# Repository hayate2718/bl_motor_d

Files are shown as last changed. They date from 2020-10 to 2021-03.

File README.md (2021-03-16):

# ブラシレスモータドライバー基板
## 機能
1. FETはTO252であれば使える。ゲート抵抗とゲートソース間コンデンサを調整すること<br>
ゲートソース間コンデンサは くらいになるようにする。
2. vdsth_pinで短絡検出を行う。パルス電流の絶対最大定格時の電圧降下を入れればいいと思う。計算式は下記 


3. ref_pinで定常の電流制限を行う。計算式は下記 


4. ピンヘッダをショートすることで動作モードの切り替えが可能<br>
jp1がfフラグを無視（オープンループでリミットを完全に外す場合はさらにRCピンをショートしてください）、jp2が高速減衰モードにできる(動くときと動かんときがある)
5. untitl.txtファイルは読んでください<br>
## 制作者コメント
<b>一枚の値段がいくらになるのか考えたくもない...結果としては4000yenほど(たけぇ<br>
このMDは制御方法が台形120度通電であるため低速域よりも高速域の効率のほうが良い。<br>
モータの最大効率運転では電流波形が正弦波に近いほどよく、台形120度通電では電流波形が台形になるように制御されているが高速域では電流波形が正弦波に近くなるため効率が良くなる。</b>

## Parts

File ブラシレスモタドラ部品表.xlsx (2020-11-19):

ブラシレスモータードライバ部品リスト
部品名 | 必要個数 | 買う場所 | 必要価格 | 単価 | 最低個数価格 | 備考(通販のコードとか)
半導体
a3930 | 1 | digikey | 722 | 722 | 722 | 620-1289-1-ND
2sc5964 | 1 | rs | 46.5 | 46.5 | 465 | 774-0746
ipd034n06ngatma1 | 6 | rs | 948 | 158 | 1580 | 825-9168
ss2040 | 1 | 秋月電子 | 15 | 15 | 300 | i02073
フルカラーRGBled | 1 | 秋月電子 | 10 | 10 | 100 | I-12726
SBR10M100P5Q | 6 | digikey | 462 | 77 | 77 | SBR10M100P5Q-13DICT-ND
ES3BB-13-F | 6 | digikey | 420 | 70 | 70 | ES3BB-FDICT-ND
fdc6305 | 1 | 秋月電子 | 12 | 12 | 120 | I-06003
抵抗 |  |  | 0
10k(1608) | 10 |  | 0
10k(集合) | 1 | 秋月電子 | 1 | 1 | 100 | p04664
47k(1608) | 2 |  | 0
39k(1608) | 1 |  | 0
22k(1608) | 1 |  | 0
33k(1608) | 2 |  | 0
1k(集合) | 1 |  | 0
10(1608) | 6 |  | 0
22(1206) | 6 | rs | 168 | 28 | 138 | 721-9680
20m(2512) | 4 | rs | 308.8 | 77.2 | 386 | 693-4384
0(1608) | 1 | 秋月電子 | 0 |  | 100 | R-11619
コンデンサ |  |  | 0
0.1u | 3 |  | 0
10u | 2 | 秋月電子 | 30 | 15 | 150 | P-13161
0.22u | 4 | 秋月電子 | 4 | 1 | 100 | P-05622
2.2u | 2 | 秋月電子 | 20 | 10 | 100 | P-14788
0.47u | 1 | 秋月電子 | 5 | 5 | 100 | 無ければP-14526これ使って
680p | 1 | 秋月電子 | 1.8 | 1.8 | 180 | P-09273
820u | 1 | rs | 107 | 107 | 535 | 843-2168
4.7n | 6 | 秋月電子 | 0 |  | 100 | P-14552
フィルムコンデンサ0.33u | 6 | rs | 156 | 26 | 660 | 896-1329
コネクタ |  |  | 0
vl3p | 1 | digikey | 111 | 111 | 111 | 455-2362-ND
xt60 | 1 | amazon | 0
ロングピンソケット8p | 2 | 秋月電子 | 0 |  | 80 | C-05779
ピンヘッダ2p | 2 | 秋月電子 | 0
zh6p L型 | 1 | 秋月電子 | 0
xh2p | 1 | 秋月電子 | 0
最低価格 |  |  | 3548.1
ブラシレスモタドラインターフェース
半導体
tlp291 | 1 | 秋月電子 | 20 | 20 | 20 | I-07189
tlp2395 | 2 | rs | 219 | 109.5 | 1095 | 885-1171
tlp290 | 1 | rs | 118 | 118 | 1180 | 885-1083
ss2040 | 1 | 秋月電子 | 15 | 15 | 300 | i02073
抵抗 |  |  | 0
1k(1608) | 10 |  | 0
4.7k(1608) | 2 |  | 0
9.1k(1608) | 2 | rs | 6.92 | 3.46 | 173 | 631-6626
コンデンサ |  |  | 0
0.1u | 3 |  | 0
コネクタ |  |  | 0
ピンヘッダ8p | 2 | 秋月電子 | 0
df1b4p | 1 |  | 0
df1b6p | 1 |  | 0
 |  |  | 378.92 |  | 9042

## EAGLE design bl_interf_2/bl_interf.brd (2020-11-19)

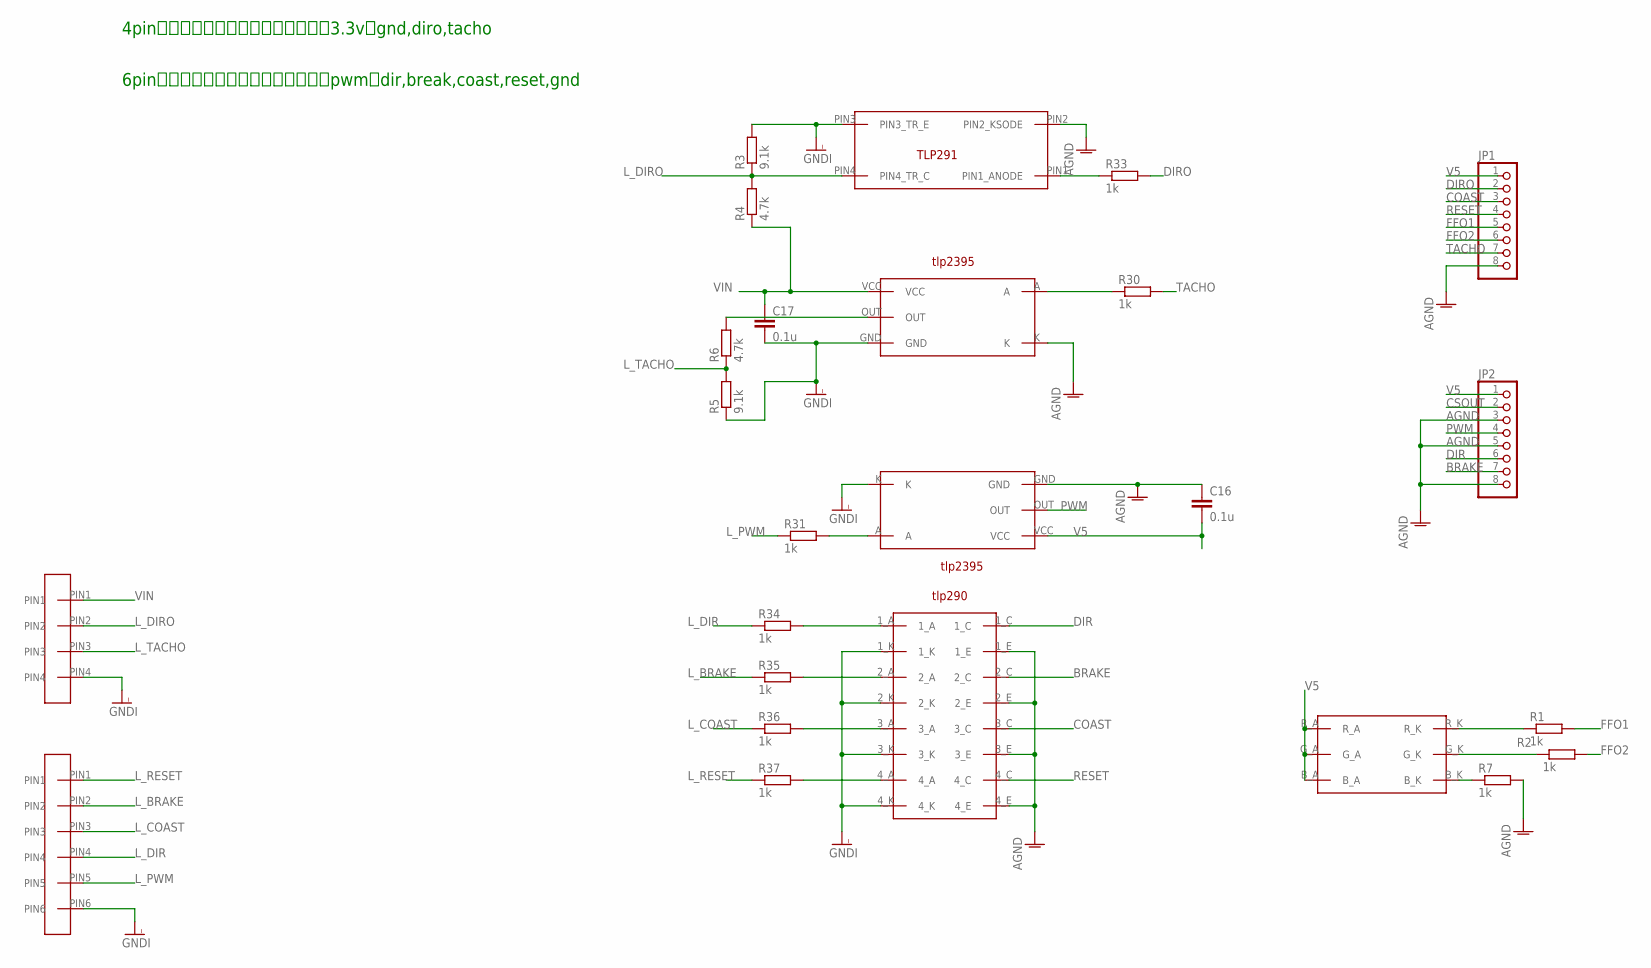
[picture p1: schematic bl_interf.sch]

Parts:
C16, C17: 0.1u; C2012
JP1, JP2: PINHD-1X8; 1X08
R1, R2, R7, R30, R31, R33, R34, R35, R36, R37: 1k; M2012
R3, R5: 9.1k; M2012
R4, R6: 4.7k; M2012
U$1: RGB_LED
U$17, U$18: TLP2395
U$19: TLP291
U$20: TLP290-4; TLP290
U$21: DF1B_L_4P
U$22: DF1B_L_6P

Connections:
AGND: C16.1, JP1.8, JP2.3, JP2.5, JP2.8, R7.2, U$17.K, U$18.GND, U$19.PIN2 (PIN2_KSODE), U$20.1_E, U$20.2_E, U$20.3_E, U$20.4_E
BRAKE: JP2.7, U$20.2_C
COAST: JP1.3, U$20.3_C
CSOUT: JP2.2
DIR: JP2.6, U$20.1_C
DIRO: JP1.2, R33.2
FFO1: JP1.5, R1.2
FFO2: JP1.6, R2.2
GNDI: C17.2, R3.2, R5.1, U$17.GND, U$18.K, U$19.PIN3 (PIN3_TR_E), U$20.1_K, U$20.2_K, U$20.3_K, U$20.4_K, U$21.PIN4, U$22.PIN6
L_BRAKE: R35.1, U$22.PIN2
L_COAST: R36.1, U$22.PIN3
L_DIR: R34.1, U$22.PIN4
L_DIRO: R3.1, R4.2, U$19.PIN4 (PIN4_TR_C), U$21.PIN2
L_PWM: R31.1, U$22.PIN5
L_RESET: R37.1, U$22.PIN1
L_TACHO: R5.2, R6.1, U$21.PIN3
unnamed: R7.1, U$1.B_K
unnamed: R1.1, U$1.R_K
unnamed: R2.1, U$1.G_K
unnamed: R30.1, U$17.A
unnamed: R31.2, U$18.A
unnamed: R6.2, U$17.OUT
unnamed: R34.2, U$20.1_A
unnamed: R33.1, U$19.PIN1 (PIN1_ANODE)
unnamed: R35.2, U$20.2_A
unnamed: R36.2, U$20.3_A
unnamed: R37.2, U$20.4_A
PWM: JP2.4, U$18.OUT
RESET: JP1.4, U$20.4_C
TACHO: JP1.7, R30.2
V5: C16.2, JP1.1, JP2.1, U$1.B_A, U$1.G_A, U$1.R_A, U$18.VCC
VIN: C17.1, R4.1, U$17.VCC, U$21.PIN1

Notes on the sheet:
4pinでモタドラからの出力を受ける。3.3vとgnd,diro,tacho
6pinでモタドラに対して入力を行う。pwmとdir,break,coast,reset,gnd

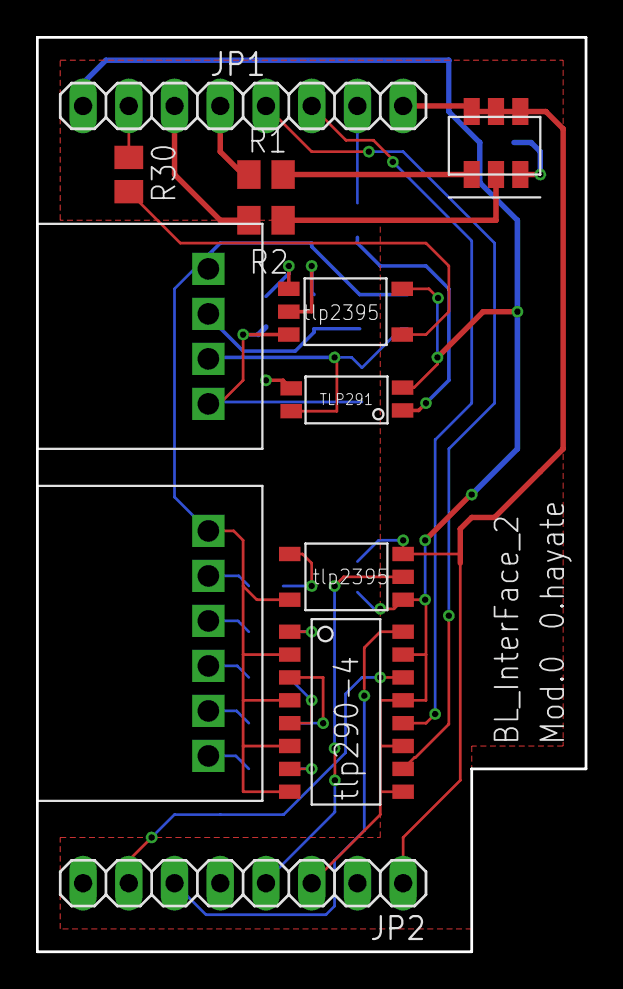
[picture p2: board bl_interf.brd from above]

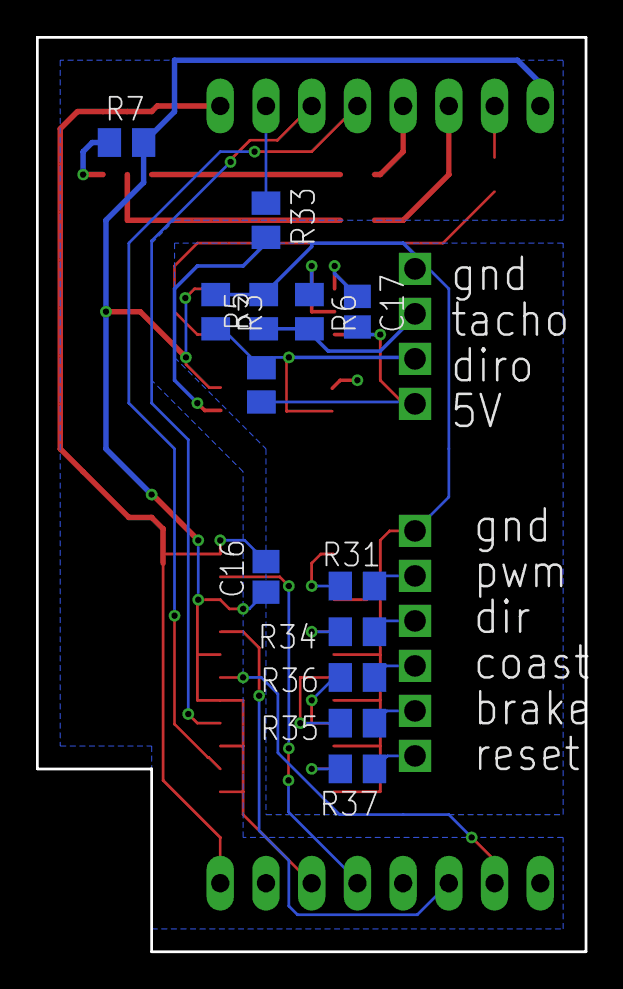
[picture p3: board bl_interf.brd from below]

Board: 2 copper layers, 30.5 x 50.8 mm, 25 parts (13 on the bottom side), 31 nets.

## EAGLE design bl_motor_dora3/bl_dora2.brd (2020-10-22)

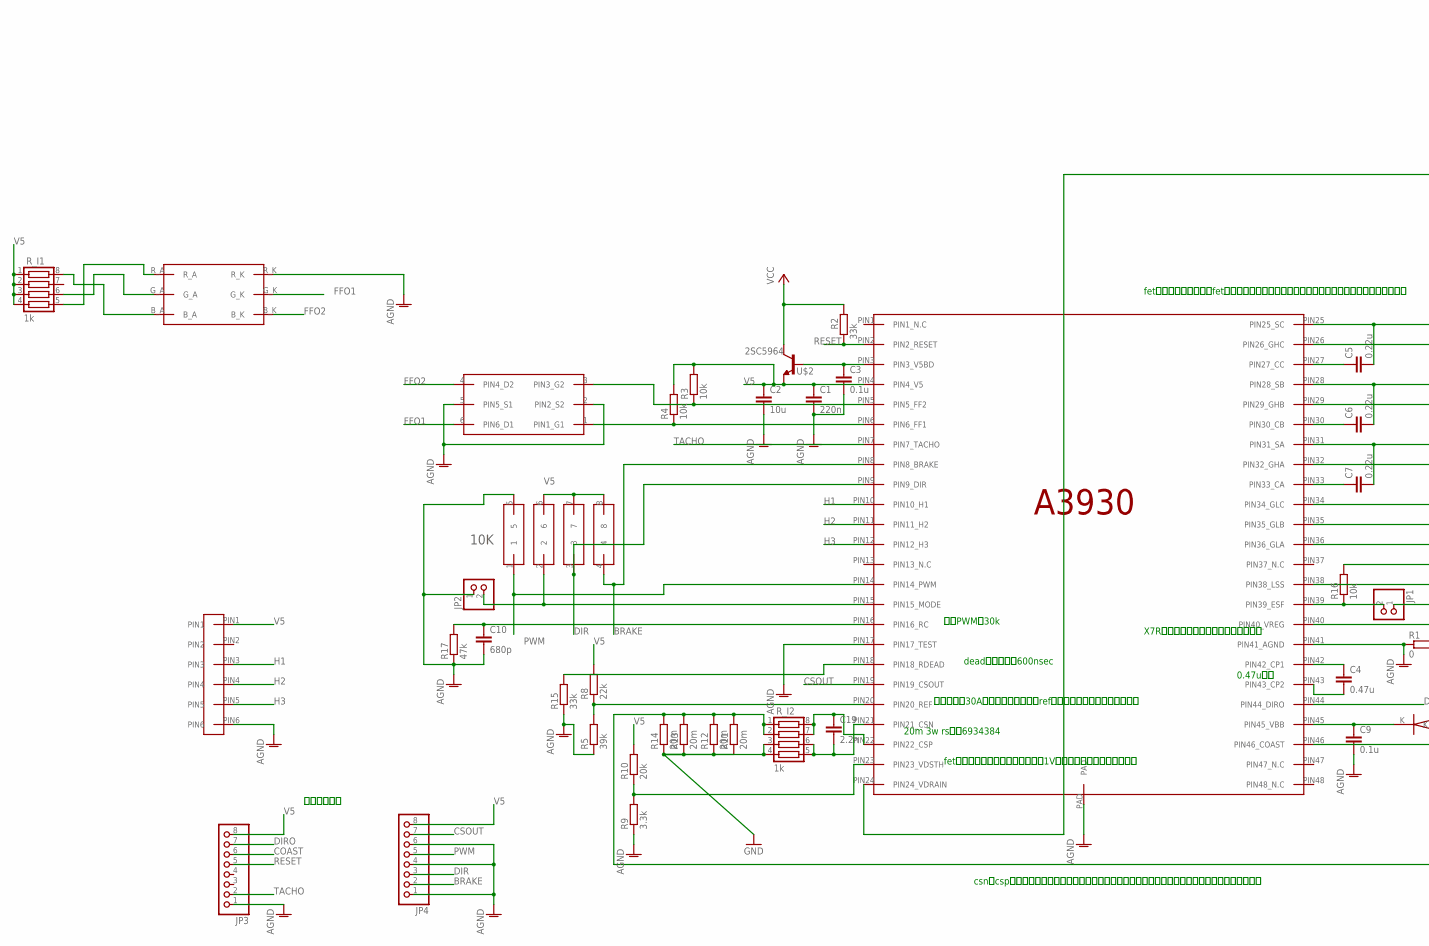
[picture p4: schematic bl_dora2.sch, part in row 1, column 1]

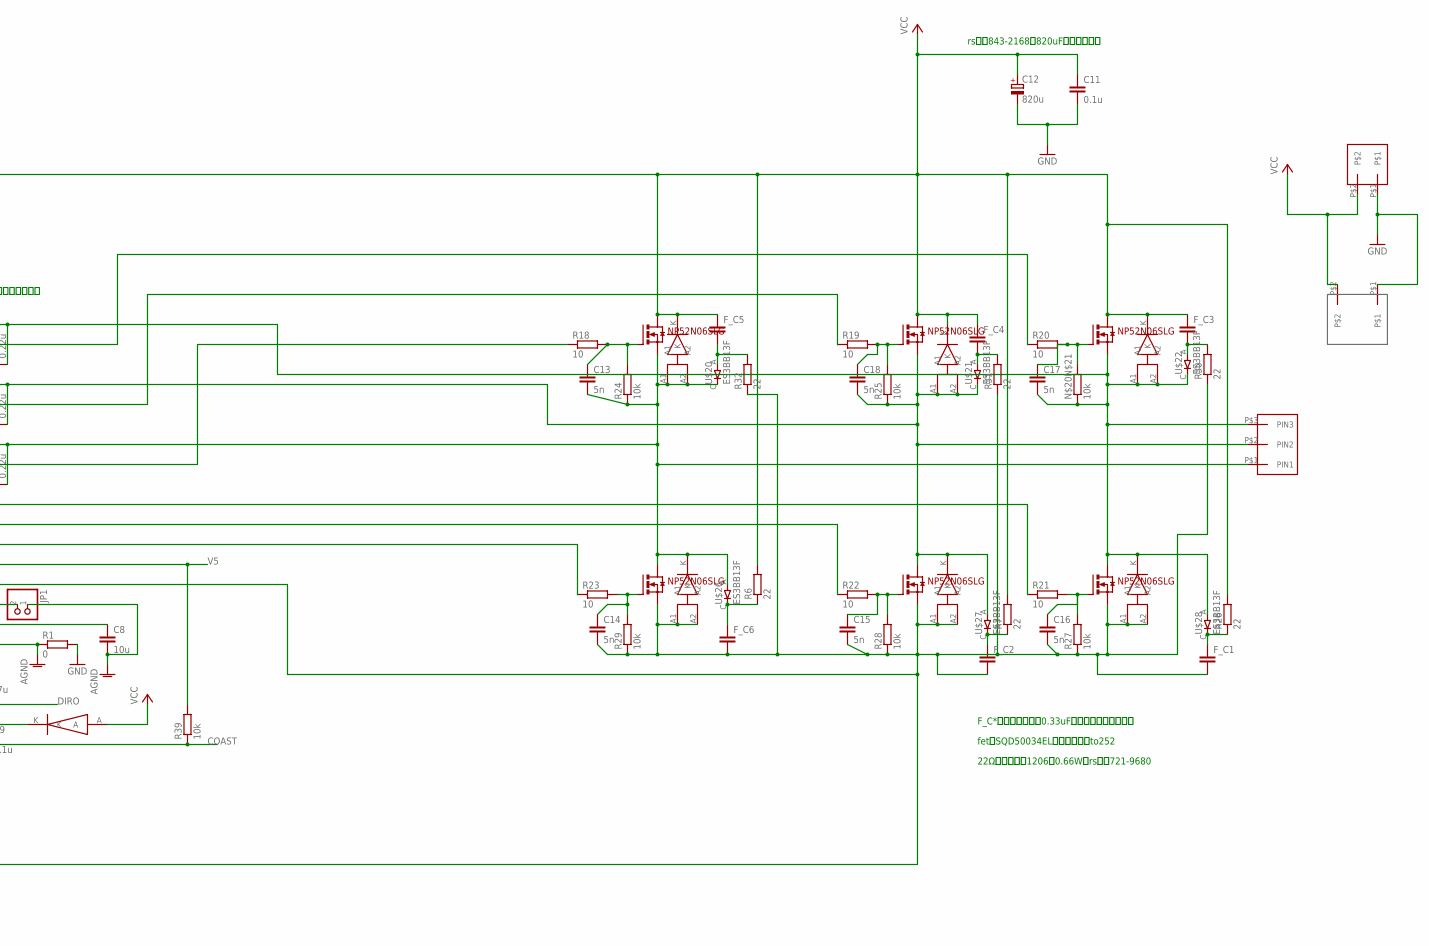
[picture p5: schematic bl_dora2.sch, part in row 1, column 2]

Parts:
C1: 220n; C2012
C2, C8: 10u; C2012
C3, C9, C11: 0.1u; C2012
C4: 0.47u; C2012
C5, C6, C7: 0.22u; C2012
C10: 680p; C2012
C12: 820u; 153CLV-1012
C13, C14, C15, C16, C17, C18: 5n; C2012
C19: 2.2n; C1608
F_C1, F_C2, F_C3, F_C4, F_C5, F_C6: FIL_CAPA
JP1, JP2: PINHD-1X2; 1X02
JP3, JP4: PINHD-1X8; 1X08
N$20N$21: 10k; M2012
R1: 0; M2012
R2, R15: 33k; M2012
R3, R4, R16, R24, R25, R27, R28, R29, R39: 10k; M2012
R5: 39k; M2012
R6, R7, R26, R30, R31, R32: 22; R1206
R8: 22k; M2012
R9: 3.3k; M2012
R10: 20k; M2012
R11, R12, R13, R14: 20m; R2512
R17: 47k; M2012
R18, R19, R20, R21, R22, R23: 10; M2012
R_I1, R_I2: 1k; 0603X4RESISTOR
U$1: A3930
U$2: 2SC5964
U$3: SSOT6_FET
U$4: RGB_LED
U$5: 10K; 1005X4RESISTOR
U$6: SMD_DAIOD
U$7, U$8, U$9, U$10, U$11, U$12: NP52N06SLG
U$13, U$14, U$15, U$16, U$17, U$18: SBR10M100P5Q
U$19: XH_2P
U$20, U$21, U$22, U$26, U$27, U$28: ES3BB13F
U$23: ZH_6P_L
U$24: XT60
U$25: VL_3P

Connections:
AGND: C1.2, C2.2, C3.2, C8.2, C9.2, C10.2, JP1.1, JP2.1, JP3.1, JP4.1, JP4.4, JP4.6, R1.1, R5.1, R9.1, R15.1, R17.1, U$1.PAD, U$1.PIN17 (PIN17_TEST), U$1.PIN41 (PIN41_AGND), U$3.2 (PIN2_S2), U$3.5 (PIN5_S1), U$4.R_K, U$5.5, U$23.PIN6
BRAKE: JP4.2, U$1.PIN8 (PIN8_BRAKE), U$5.4
COAST: JP3.6, R39.1, U$1.PIN46 (PIN46_COAST)
CSOUT: JP4.7, U$1.PIN19 (PIN19_CSOUT)
DIR: JP4.3, U$1.PIN9 (PIN9_DIR), U$5.3
DIRO: JP3.7, U$1.PIN44 (PIN44_DIRO)
ESF: JP1.2, R16.1, U$1.PIN39 (PIN39_ESF)
FFO1: U$3.6 (PIN6_D1), U$4.G_K
FFO2: U$3.4 (PIN4_D2), U$4.B_K
GND: C11.2, C12.-, R1.2, R11.1, R12.1, R13.1, R14.1, R_I2.3, R_I2.4, U$19.P$1, U$24.P$1
H1: U$1.PIN10 (PIN10_H1), U$23.PIN3
H2: U$1.PIN11 (PIN11_H2), U$23.PIN4
H3: U$1.PIN12 (PIN12_H3), U$23.PIN5
unnamed: C3.1, U$1.PIN3 (PIN3_V5BD), U$2.B
unnamed: R3.1, U$1.PIN5 (PIN5_FF2), U$3.3 (PIN3_G2)
unnamed: R4.1, U$1.PIN6 (PIN6_FF1), U$3.1 (PIN1_G1)
unnamed: R15.2, U$1.PIN18 (PIN18_RDEAD)
unnamed: F_C5.P$2 (2), R32.2, U$20.A
unnamed: C14.2, C15.2, C16.2, F_C1.P$2 (2), F_C2.P$2 (2), F_C6.P$2 (2), R11.2, R12.2, R13.2, R14.2, R27.1, R28.1, R29.1, R30.1, R31.1, R32.1, R_I2.1, R_I2.2, U$1.PIN38 (PIN38_LSS), U$8.PIN3_S, U$10.PIN3_S, U$12.PIN3_S, U$14.A1, U$14.A2, U$15.A1, U$15.A2, U$18.A1, U$18.A2
unnamed: R5.2, R8.1, U$1.PIN20 (PIN20_REF)
unnamed: C19.2, R_I2.5, R_I2.6, U$1.PIN21 (PIN21_CSN)
unnamed: R9.2, R10.1, U$1.PIN23 (PIN23_VDSTH)
unnamed: R_I1.5, U$4.R_A
unnamed: C4.1, U$1.PIN42 (PIN42_CP1)
unnamed: JP2.2, U$1.PIN15 (PIN15_MODE), U$5.2
unnamed: C4.2, U$1.PIN43 (PIN43_CP2)
unnamed: C5.1, U$1.PIN27 (PIN27_CC)
unnamed: C6.1, U$1.PIN30 (PIN30_CB)
unnamed: C7.1, U$1.PIN33 (PIN33_CA)
unnamed: C7.2, C13.2, R24.1, U$1.PIN31 (PIN31_SA), U$7.PIN3_S, U$8.PIN2_D, U$13.A1, U$13.A2, U$14.K, U$20.C, U$25.P$1 (PIN1), U$26.A
unnamed: C19.1, R_I2.7, R_I2.8, U$1.PIN22 (PIN22_CSP)
unnamed: R_I1.6, U$4.G_A
unnamed: C8.1, U$1.PIN40 (PIN40_VREG)
unnamed: C9.1, U$1.PIN45 (PIN45_VBB), U$6.K
unnamed: C10.1, R17.2, U$1.PIN16 (PIN16_RC)
unnamed: C13.1, R18.2, R24.2, U$7.PIN1_G
unnamed: C18.1, R19.2, R25.2, U$9.PIN1_G
unnamed: C17.1, N$20N$21.2, R20.2, U$11.PIN1_G
unnamed: C16.1, R21.2, R27.2, U$12.PIN1_G
unnamed: C15.1, R22.2, R28.2, U$10.PIN1_G
unnamed: C14.1, R23.2, R29.2, U$8.PIN1_G
unnamed: R23.1, U$1.PIN36 (PIN36_GLA)
unnamed: R22.1, U$1.PIN35 (PIN35_GLB)
unnamed: R21.1, U$1.PIN34 (PIN34_GLC)
unnamed: R_I1.8, U$4.B_A
unnamed: R18.1, U$1.PIN32 (PIN32_GHA)
unnamed: R19.1, U$1.PIN29 (PIN29_GHB)
unnamed: R20.1, U$1.PIN26 (PIN26_GHC)
unnamed: F_C4.P$2 (2), R31.2, U$21.A
unnamed: F_C3.P$2 (2), R30.2, U$22.A
unnamed: F_C6.P$1 (1), R6.1, U$26.C
unnamed: C5.2, C17.2, N$20N$21.1, U$1.PIN25 (PIN25_SC), U$11.PIN3_S, U$12.PIN2_D, U$17.A1, U$17.A2, U$18.K, U$22.C, U$25.P$3 (PIN3), U$28.A
unnamed: F_C1.P$1 (1), R26.1, U$28.C
unnamed: F_C2.P$1 (1), R7.1, U$27.C
unnamed: C6.2, C18.2, R25.1, U$1.PIN28 (PIN28_SB), U$9.PIN3_S, U$10.PIN2_D, U$15.K, U$16.A1, U$16.A2, U$21.C, U$25.P$2 (PIN2), U$27.A
PWM: JP4.5, U$1.PIN14 (PIN14_PWM), U$5.1
RESET: JP3.5, R2.1, U$1.PIN2 (PIN2_RESET)
TACHO: JP3.2, U$1.PIN7 (PIN7_TACHO)
V5: C1.1, C2.1, JP3.8, JP4.8, R3.2, R4.2, R8.2, R10.2, R16.2, R39.2, R_I1.1, R_I1.2, R_I1.3, R_I1.4, U$1.PIN4 (PIN4_V5), U$2.E, U$5.6, U$5.7, U$5.8, U$23.PIN1
VCC: C11.1, C12.+, F_C3.P$1 (1), F_C4.P$1 (1), F_C5.P$1 (1), R2.2, R6.2, R7.2, R26.2, U$1.PIN24 (PIN24_VDRAIN), U$2.C, U$2.C@2 (C), U$6.A, U$7.PIN2_D, U$9.PIN2_D, U$11.PIN2_D, U$13.K, U$16.K, U$17.K, U$19.P$2, U$24.P$2

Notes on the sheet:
20m 3w rs品番6934384
0.47u以上
deadタイムは約600nsec
内部PWMは30k
csnとcspはできるだけ同じ長さで同じルート・無理にくねくねさせるなら同じながさでなくていい
ピンソケット
X7Rなどの特性のよいものをつかうこと
fetを変えた場合はそのfetのゲート容量によってブートストラップコンデンサを変えること
rs品番843-2168の820uFのコンデンサ
F_C*のコンデンサは0.33uFのフィルムコンデンサ
fetにSQD50034ELを使う。同じto252
電流制限は30Aに設定されている。refの抵抗比を変えることで変更可
fetのドレインソース間がオン時に1Vを超えたら短絡とみなされる
22Ωの抵抗器は1206の0.66W。rs品番721-9680

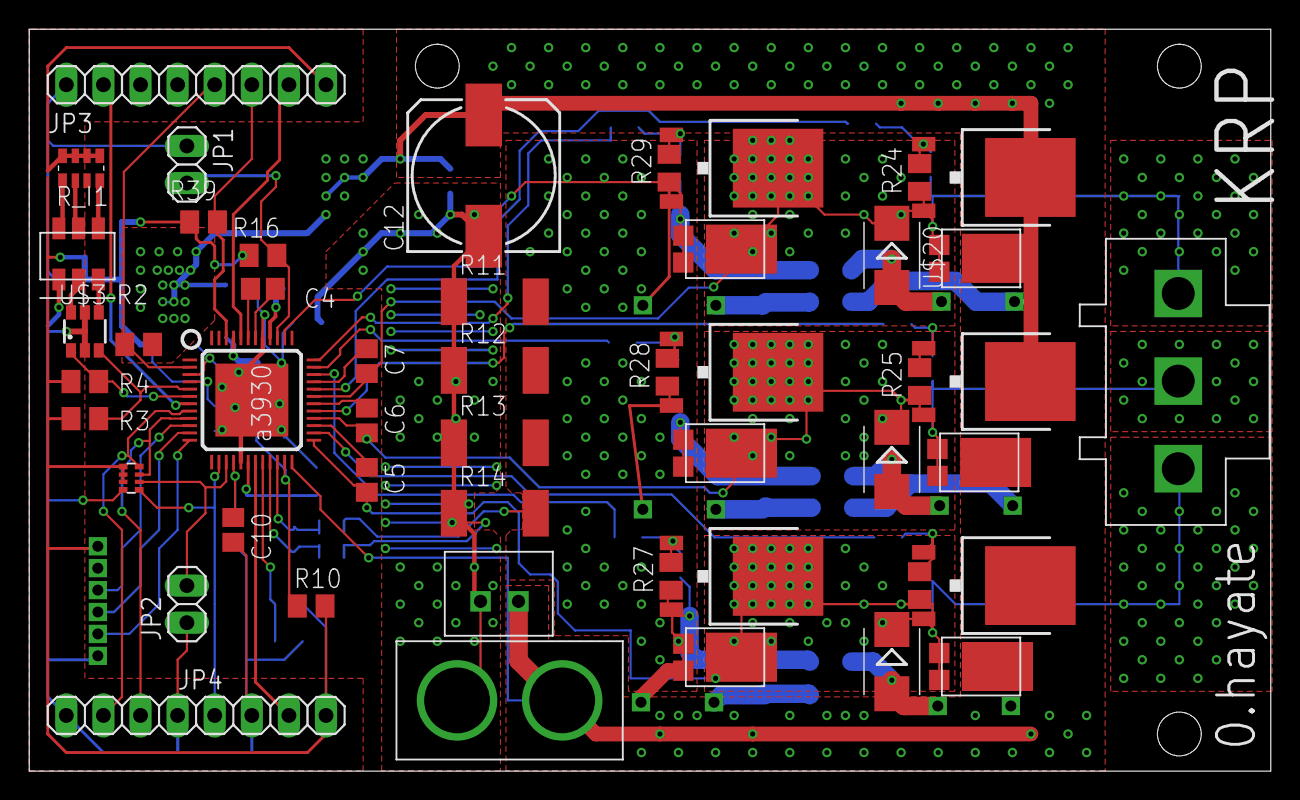
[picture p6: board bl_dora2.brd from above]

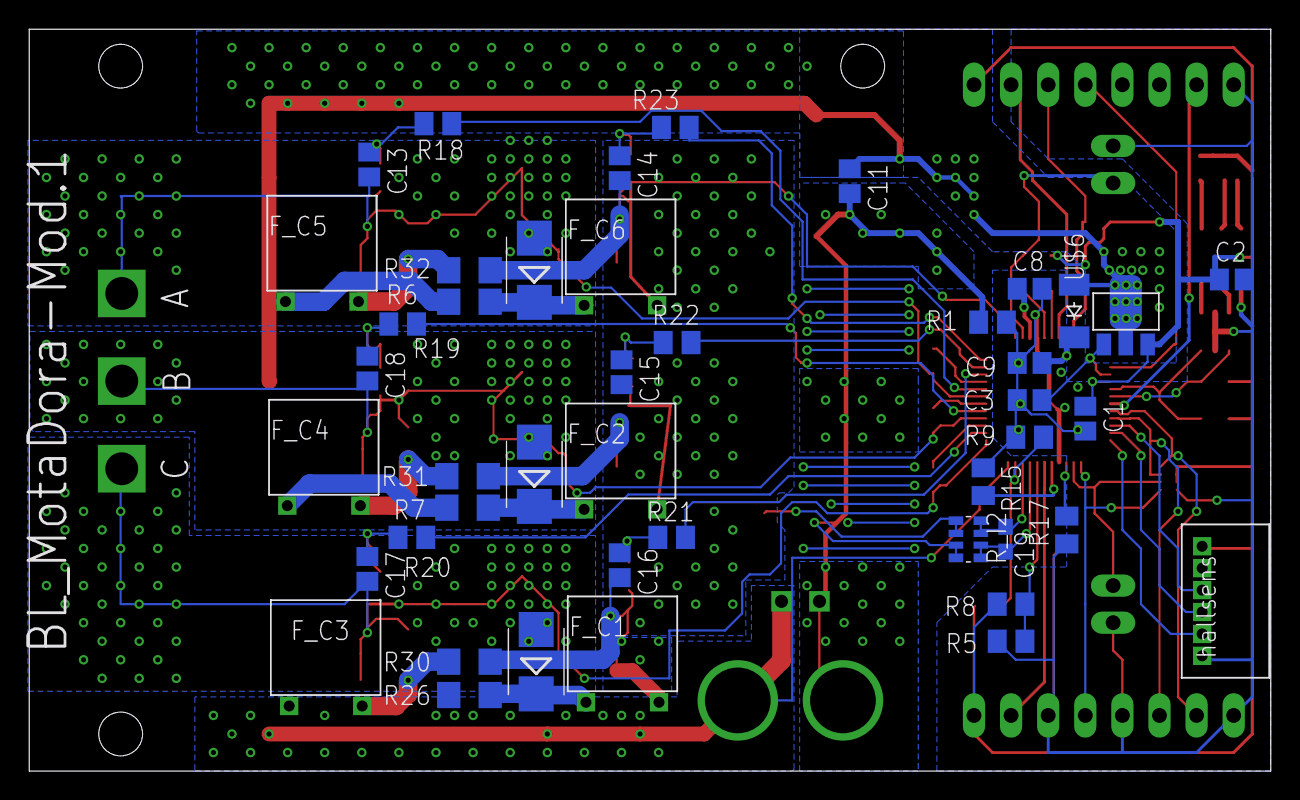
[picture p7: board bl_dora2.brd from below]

Board: 2 copper layers, 85.0 x 50.8 mm, 93 parts (44 on the bottom side), 60 nets.

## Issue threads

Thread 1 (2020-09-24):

基板固定用の穴がない

TakashiKusachi, 2020-09-24:
基板固定用の穴がないのは実用上かなり厳しい。
* 基盤がケーブルに引っ張られて飛ぶ。
* 「後でつける」は永遠とやらない（体験談）

最低でも三か所で固定できるようにした方がいいです。（二か所はその線を軸に回転がかかって固定側が壊れる）

TakashiKusachi, 2020-09-29:
ドリル穴3はM2にしてはでかいしM3にしては小さいから2.7mmとか2.3mmとかにした方がいい

Closed 2020-10-05.

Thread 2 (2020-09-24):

PWM周波数について

TakashiKusachi, 2020-09-24:
アバランシェ破壊したのでは？ということでしたが、一度確認したい点が一つ。
PWM周波数はいくつで設定しましたか？

BLDCの場合、PWM周波数が高くても低くてもMOSFETには危ないので気を付けてください。

hayate2718, 2020-09-25:
pwm周波数は50kHzです。理由としては、自分のpwm発生道具が50kHzでプログラム書き直すのめんどくさかったというのが大きかったのですが、a3930のデモボードの回路図をみて内部pwm周波数が40kHzで設定されており、外部pwmで動かすときは内部pwm周波数よりも高くするということだったので50kHzで問題ないだろうと判断しました。

hayate2718, 2020-09-25:
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

pwm周波数は50kHzです。理由としては、自分のpwm発生道具が50kHzでプログラム書き直すのめんどくさかったというのが大きかったのですが、a3930のデモボードの回路図をみて内部pwm周波数が40kHzで設定されており、外部pwmで動かすときは内部pwm周波数よりも高くするということだったので50kHzで問題ないだろうと判断しました。

TakashiKusachi, 2020-09-25:
なるほど。おおよそ問題ないかと。
Rgを大きくしたみたいなので、デッドタイムとの兼ね合いを気を付けてください。
軽く設計を見た限りt_deatが2.84(1.42 * 2)us、PWMが20um(50kHz)なので結構近くなってる。現状でduty10%未満はほとんど回らないことになっている。これだと低速回転時に安定しないので、設計を見直した方がいいかもしれない。

### Rgを大きくするときの注意
1. Rgを大きくする
2. スイッチングに時間がかかる
3. デッドタイムを大きくする必要がある。
4. PWM一周期あたりのデッドタイムの割合が増える
5. 低duty、高dutyの線形性がなくなる。
6. 制御性ポンコツ

対策
1. PWM周波数を下げる。
2. デッドタイムを短くする。

デッドタイムの設計はなんかの資料を参考にしてほしいですが、ゲートの挙動をオシロで見るのが早いです。ただ、オシロが使えない現状では、LTSpiceかなんかのシミュレータで挙動をみてもいいかもしれないですね。

TakashiKusachi, 2020-09-25:
追記で
先日の報告会でH氏から、フリーホイーリングダイオードについて聞かれてましたが、bodyDで済ませているという回答を聞きました。
電流の小さいアプリケーションではbodyDで問題ないです。が、電流の大きいアプリケーションでは、少し問題が現れます。

まず、bodyDはフリーホイーリングのためにあるわけではないという認識をもってほしいです（あれはMOSFETの構造上表れているだけ）。このため、フリーホイーリングの目的に対応した特性としては糞です。重要な特性は二つ（というよりこれ以外書いてないけど
* 逆回復時間
* Vf（順方向起電圧）

デッドタイム中はこのフリーホイーリングDを通って電流が還ります。このため、Vfが大きいとその分損失が大きいことになります。またデッドタイムからローサイドをオープンするとき、ハイサイドのDは順方向（S->D)から逆方向へと電圧が変わるわけですが、この時結構電流が流れます。この時間が逆回復時間です。つまりハイサイドとローサイドが両方ともオープンになる貫通の時間があって、これがローサイドを大きく発熱させます。

長くなりましたが、bodyDはそこまで気を遣った特性ではないためこの点を注意した方がいいということです。逆回復時間は電流に相関があるため、電流が小さい限りは問題ないです。

以上知っていたら、長文失礼しました。

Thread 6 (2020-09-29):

シャントの配線があまりよろしくない

TakashiKusachi, 2020-09-29:
## 低抵抗シャントでの電流測定の配線があまりよろしくない
低抵抗の電流計測はアナログ回路としてかなり丁寧に設計しないと実はろくに使えたものじゃないので注意してください。

### 抵抗器と分岐点の間にできるだけ電流を流さないこと
電流測定に重要なことは信用できる抵抗値であり、これを達成するにはパターンの抵抗自体考慮する必要があります。このため下図のように、電流が流れるルートから切り離して測定用のパターンを伸ばす必要があります。
少し話は変わってしまいますが、４端子抵抗測定法などを調べてみると勉強になるかも
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
この距離が良くないという話。
### ただし、そもそも抵抗器が5%...
なので気にしなくてもいいかも。

## 配線の長さをそろえる部分について
多分いらない。配線の長さをそろえるのは、主にデジタルの高速信号の場合だけです。配線長の偏差が信号の周期の定数倍以上になると周期がずれて信号が正確に読み取れなくなりますが、アナログで低速である限りは必要ないです。
また、上の話を考慮したくなるかもしれないですが、この信号線に流れる電流は微量（入力インピーダンスが高い）です。なので、配線の長さをそろえてインピーダンスをそろえる必要はないです。一方で電流が小さいからこそ、ノイズに弱い信号線になります。下手にくねくねさせた方が危ない。

TakashiKusachi, 2020-09-29:
追記。データシートにながさ揃えろって書いてあるのか…
こんな露骨にくねくねさせるよりは、自然に長さがそろうようにした方がいいかと。図のような配線なら勝手に合うはず

hayate2718, 2020-09-29:
測定点までの距離を同じくらいにするために0Ω抵抗を使って測定用の配線を作ってみます。くねくねさせて無理やりそろえるくらいだったら多少の誤差は無視したほうが良いですか？

TakashiKusachi, 2020-09-29:
0オーム？

多少はね。無視してもいいんじゃないかな

Closed 2020-10-05.

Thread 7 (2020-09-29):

RCDスナバのDについて

TakashiKusachi, 2020-09-29:
## RCDスナバのDはショットキーバリア(SBD)よりpn接合型ダイオードの方がいいと思う
RCDスナバのDとしては逆回復特性や降伏電圧の高いpn接合のD（ファストリカバリーダイオード(FRD)と呼ばれている種類）の方がいいはずなのでそれに変えた方がいいと思います。それからスナバ回路にはそんな大電流流れないのでもっと小さいのでも大丈夫では？

そもそもスナバいる？

hayate2718, 2020-09-29:
このダイオードの逆回復時間が18nsecで降伏電圧が100Vなのですが、具体的にどのくらいの逆回復時間と降伏電圧のものを選んだほうが良いですか？スナバ回路ってそんなに大電流流れないのですね...瞬間電流100Aほど流せるドライバにしたかったので瞬間電流の最大定格をその倍取っていました。スナバ回路はこれつけとけばfet保護は完璧だろうというノリでつけました。

TakashiKusachi, 2020-09-29:
こいつショットキーバリアダイオード（SBD)じゃなくてDIODES社商標のスーパーバリアダイオードとかいう特殊なやつなのか…
同様にSBDの代替で開発されたものみたいで、高逆回復特性、低vfが特徴みたいだけど、この用途なら低vfは必要ないからもう少し小さくて安いやつでも大丈夫じゃない？というコストのお話になる。それことフリーホイーリングD(FWD)がないのは問題なので、スナバにこんなデカい領域使うなら変えた方がいいと思う。

TakashiKusachi, 2020-09-29:
https://toshiba.semicon-storage.com/info/docget.jsp?did=13411
これ見てみた？

hayate2718, 2020-09-29:
一応見たことあります。スナバの設計に使った資料は添付した二つのファイルです。
[sic-mos_snubber_circuit_design_an-j.pdf](https://github.com/hayate2718/bl_motor_d/files/5301074/sic-mos_snubber_circuit_design_an-j.pdf)
[RH984b_05.pdf](https://github.com/hayate2718/bl_motor_d/files/5301075/RH984b_05.pdf)

hayate2718, 2020-09-29:
現在スナバに使ったダイオードはフリーホイールダイオードに使える性能していますか？一応スナバに関してはどの程度の電流が流れるのかわからなくてかなり多く見積もっていたので、電流がそれほど流れないのであればもともと採用しようとしていた小さいダイオードがあるのでそれを用います。

TakashiKusachi, 2020-09-29:
富士電機のはIGBTなことを考えるとおそらく数十kW級のアプリケーションな気がする。実際例で一番小さいので30kWとかロボコンの範疇じゃない。主回路浮遊インダクタンスも＞100V級の回路は絶縁距離を保たないといけない特性上大きく出ます。多分このくらいの回路だと数十nH大きくても数十nHくらいでしょう。電流に関しては定常100A取ってるのは現実できじゃないことを考慮しても50A,20kHzで1/4Wの抵抗で大丈夫じゃないかな。
ダイオードの損失設計はわからん。けど、定格電流なんで定常の場合がほとんどだから、瞬間電流が定格超えても問題ない場合がほとんど

FWDにはスーパーバリアダイオードは非常に適していると思います。

TakashiKusachi, 2020-09-29:
#2 の話に戻るけど、正直アバランシェ破壊はもっとこう電力アプリケーションに入ってからの話な気がしていて、それ以前にFWDがないせいで熱損失破壊してるだけじゃないかと思ってる。

Closed 2021-07-26.

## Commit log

2020-09-23 ブラシレスモタドラ
    別途インターフェース基板を作らないと動きません
    [bl_dora2.brd, bl_dora2.sch]
2020-09-28 開発途中
    [bl_dora2.brd, bl_dora2.sch]
2020-09-29 一応完成したもの
    fetにスナバ回路を加えることによりモーターサージを吸収できるようにした。ゲート・ソース間にコンデンサを入れられるようにして、セルフターンオンしないように細かく調整できるようにした。デッドタイムの設計を変え忘れた。確か47kΩでデッドタイムが700nSecほどになる。空冷するためのファン用のコネクタを追加した。還流ダイオードを入れるスペースが作れなかった。この設計で実験し思う性能が出せない場合は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
    [bl_dora2.brd, bl_dora2.sch]
2020-09-29 フィードバックを受けて修正したもの
    スナバを大幅に修正して非放電型スナバにした。これにより抵抗器の損失を少なくできるため小型の抵抗器が使えるようになった。スナバに使っていたダイオードを還流ダイオードに使用して、スナバのダイオードは小さめのものに変えた。電流センサ用の配線をくねくねしないで揃うように頑張った。非放電型スナバの周りの配線が複雑になって怪しい気がするのでチェックお願いします。
    [bl_dora2.brd, bl_dora2.sch]
2020-09-30 配線修正
    シャントの配線をしっかり切り分ける。
    [bl_dora2.brd, bl_dora2.sch]
2020-10-01 完成品
    配線の修正などをおこなった
    [bl_dora2.brd, bl_dora2.sch]
2020-10-07 スケマティックの抵抗の値がおかしかったので更新した
    [bl_dora2.brd, bl_dora2.sch]
2020-10-07 スケマチックの抵抗の値がおかしかった
    [bl_dora2.brd, bl_dora2.sch]
2020-10-17 エンハンスドver
    [bl_dora2.brd, bl_dora2.sch]
2020-10-22 シャント抵抗ラインにローパスフィルタの追加
    電流制限、電流測定がつかいもんにならんかったからノイズを消すためにローパスフィルタをシャント抵抗の電位差を測るラインに追加
    [bl_dora2.brd, bl_dora2.sch]
2020-11-19 ブラシレスモータインタフェース基板
    3.3vだけで動作するように昇圧回路のっけてたけど無駄だからやめた
    [bl_interf.brd, bl_interf.sch]
